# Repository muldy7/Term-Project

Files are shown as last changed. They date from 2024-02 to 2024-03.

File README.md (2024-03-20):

# Term-Project
Introduction 

This repository includes the code and documentation for the ME 405 Lab "Learn by Dueling" term project. The goal of this project was to create an automated foam dart turret to participate in a dueling competition. The turret had certain required functionality including the use of 1 brushed DC motor with encoder, another DC motor of the team's choice, and MLX90640 infrared camera supporting I2C communication. The turret is designed specifically for use in the ME 405 lab duel and operated by the team members. 

Hardware Design:  

The hardware system was designed to be robust and simple. Its main features include a panning axis controlled by a brushed DC motor with encoder feedback, a manually adjusted tilt secured by a bold, and servo-controlled trigger activation. The blaster used is a Nerf Strongarm revolving magazine and is manually cocked before each shot. The base is laser cut from 1/8th inch acrylic sheet and secures the motor and turntable relative to each other. The motor housing, gears, panning structure, camera mount, and trigger arm are 3D printed PLA. The camera was attached to the robot using the rail on the Nerf gun, along with 3D printed parts and a GoPro mount.  

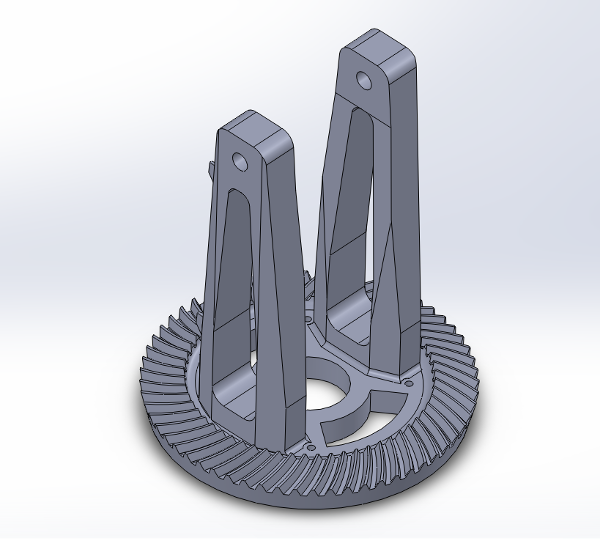
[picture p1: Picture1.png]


Figure 1: SolidWorks model of the turret base with a built-in bevel gear for rotation 

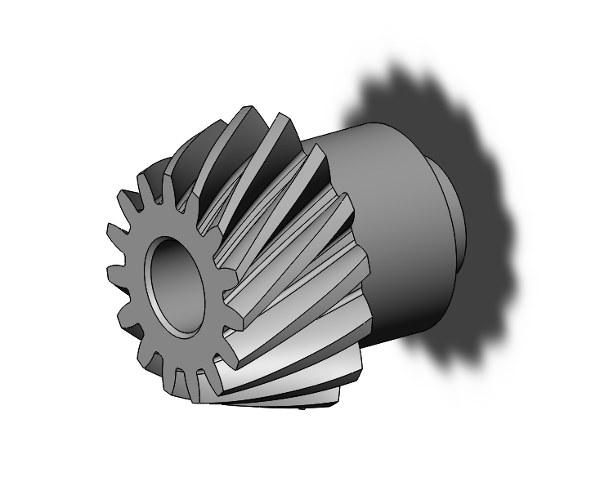
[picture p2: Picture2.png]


Figure 2: Pinion for the assembly 

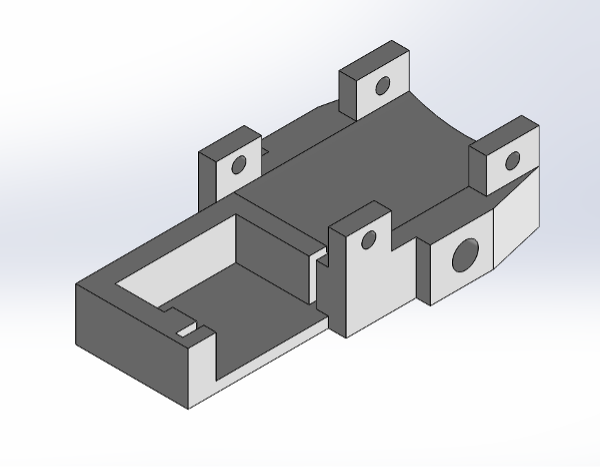
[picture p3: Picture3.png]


Figure 3: SolidWorks model of our Nerf gun mount  

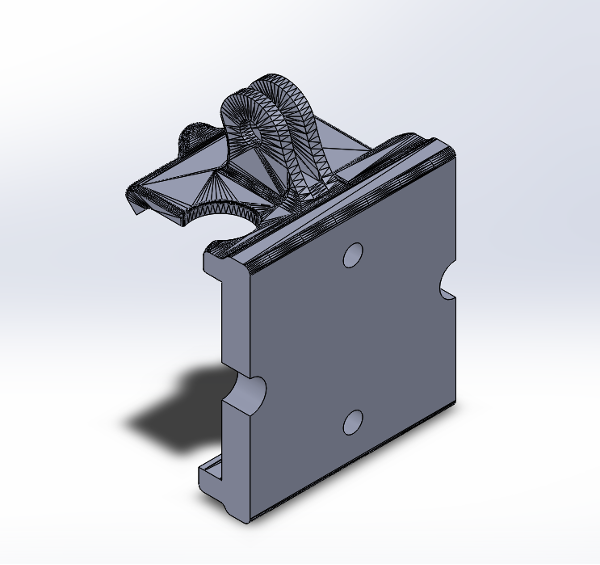
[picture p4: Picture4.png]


Figure 4: SolidWorks model of our camera mount  

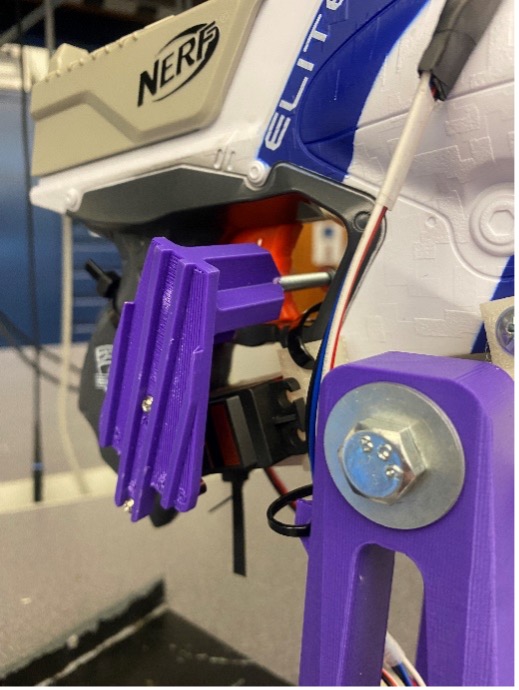
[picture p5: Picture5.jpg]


Figure 5. Trigger pull mechanism 

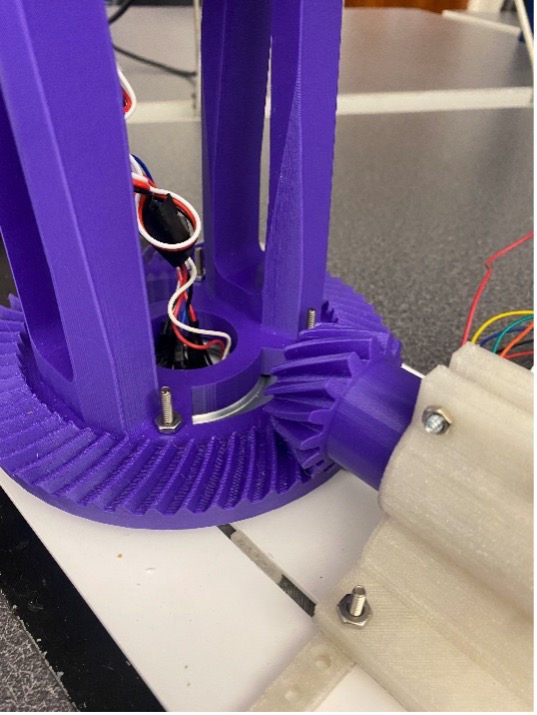
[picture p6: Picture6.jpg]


Figure 6. Panning axis mechanism. DC motor to panning structure on rotatory bearing.  

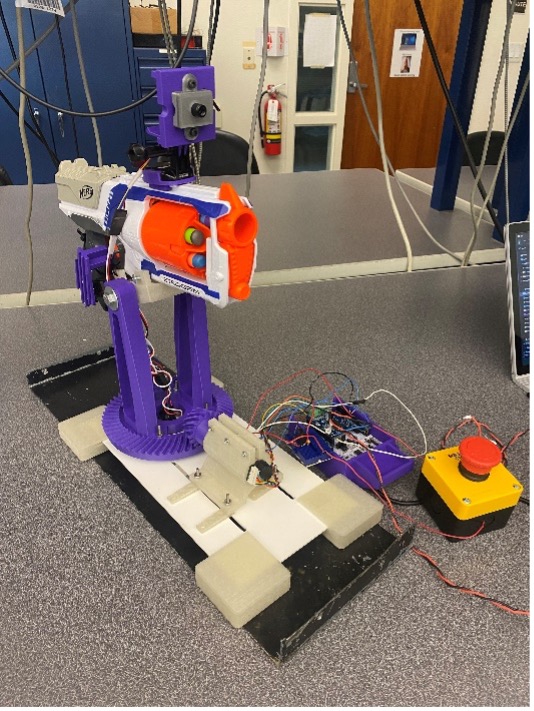
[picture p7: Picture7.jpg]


Figure 7. Entire hardware system 

Other hardware implementations include the addition of an emergency stop button and voltage regulator for the servo. The voltage regulator was used to supply the servo with 6V without the need for a second voltage source. The circuit was implemented as shown below with the input as 12V from the voltage source and the output to the servo.  

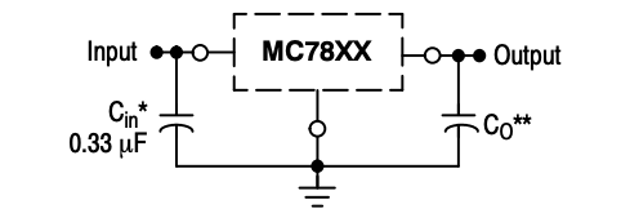
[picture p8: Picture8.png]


Source: https://www.mouser.com/datasheet/2/308/1/MC7800_D-2315963.pdf 

Software Design:   

The software includes a main file which implements cooperative multitasking and integrates all classes and functions created previously to use the hardware.  

The hardware classes are the encoder reader, motor drover, MLX cam, and servo driver. A PD controller class was created and used for the closed loop motor control.   

The main files include a camera task and a controller class which are implemented as finite state machines with cooperative multitasking using the task_share.py and cotask.py classes provided.  

The main file was designed around the finite state machines seen below. There were two main tasks in the file, one to control the turret and the other to take images with the camera.  The two tasks were designed to run through one cycle after the main program is run. 

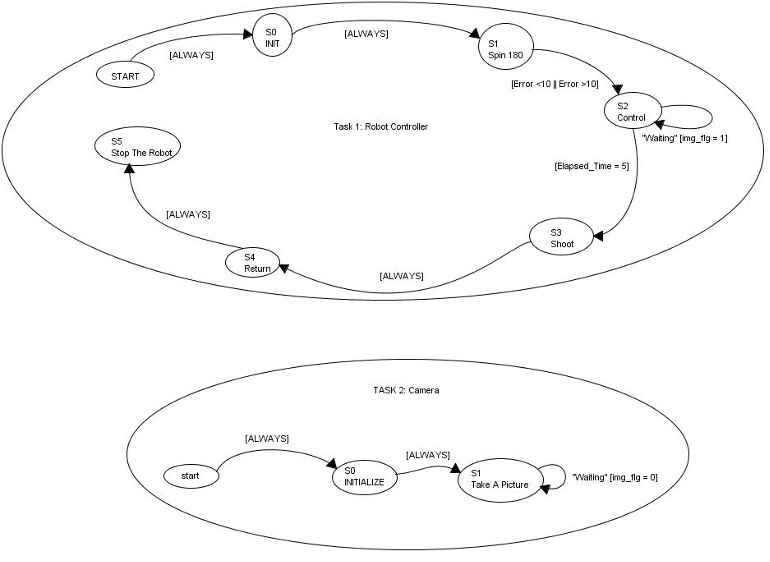
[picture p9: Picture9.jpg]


Figure: 8. Finite State Machines for the two tasks. 

Results: 

The robot won lab section 05 single elimination dueling tournament by eliminating 3 opposing teams. In each successive round our accuracy increased as we changed the algorithm parameters. The scoring criteria are as follows: First team to hit=3 points, second team to hit=1 point, no shoot=0 points, miss=-1. In the first round we scored net 0 points, and the last round we scored a net 8 points in 5 rounds.  

The following day during open competition, our robot remained undefeated and successfully hit opposing teams 10/12 times.  

We learned that the most important aspect to competition success was refinement of the targeting algorithm. Through the closed loop motor control, the gun was able to aim very accurately where it “wanted” but having this setpoint agree with the human target location was difficult. To have the setpoint algorithm more accurately find the target, a few additions were made to the algorithm.  One included limiting the field of view of the camera to above the table and within the left and right edges. Also, a filter was applied to all thermal data to eliminate any values lower than 300 to reduce background noise affecting the targeting. Lastly, the final setpoint was calculated based on a 5 columns centroid calculation around the hottest column of thermal data.  

This project has a lot of potential for future work and development, including improvements to the cooperative multitasking for more continuous feedback and thermal data processing. Also, a tilt axis for a full range of aiming would be a great hardware improvement.

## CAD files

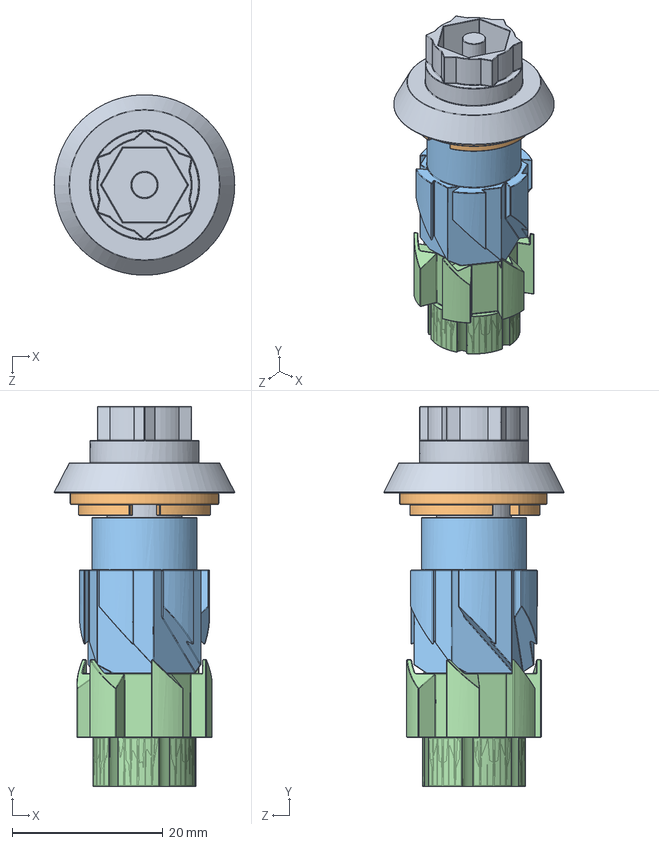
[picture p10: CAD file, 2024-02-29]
3D_models/nerf gun/Assem1.SLDASM
24.0 x 50.5 x 24.0 mm
Spin Lock
Spin Ring
Rotation 2
Rotation 1

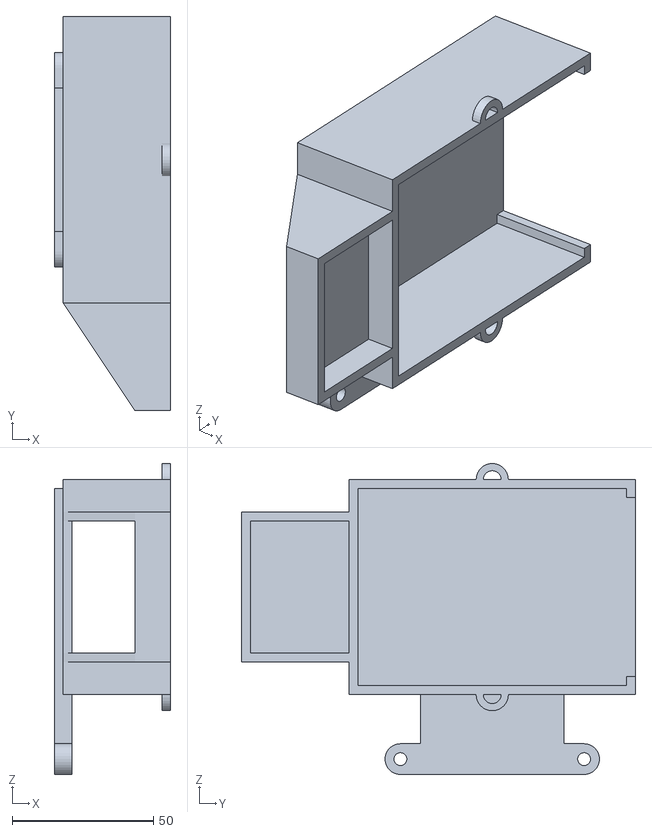
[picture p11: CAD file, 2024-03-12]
3D_models/assembly/CPU Holder v4.stl
41.3 x 139.7 x 110.2

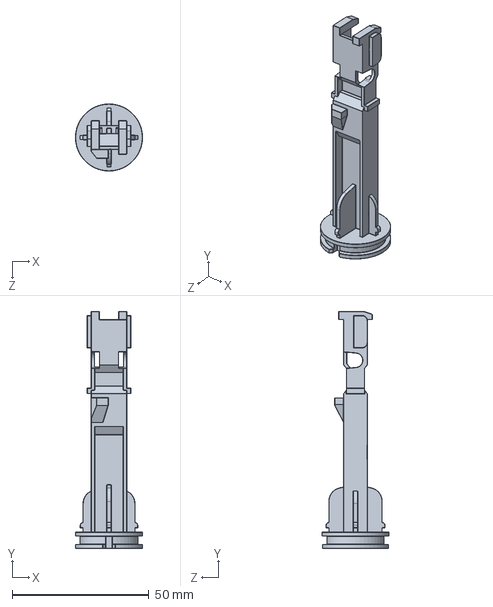
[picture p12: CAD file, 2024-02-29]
3D_models/nerf gun/Tower.SLDPRT
24.5 x 86.5 x 24.5 mm

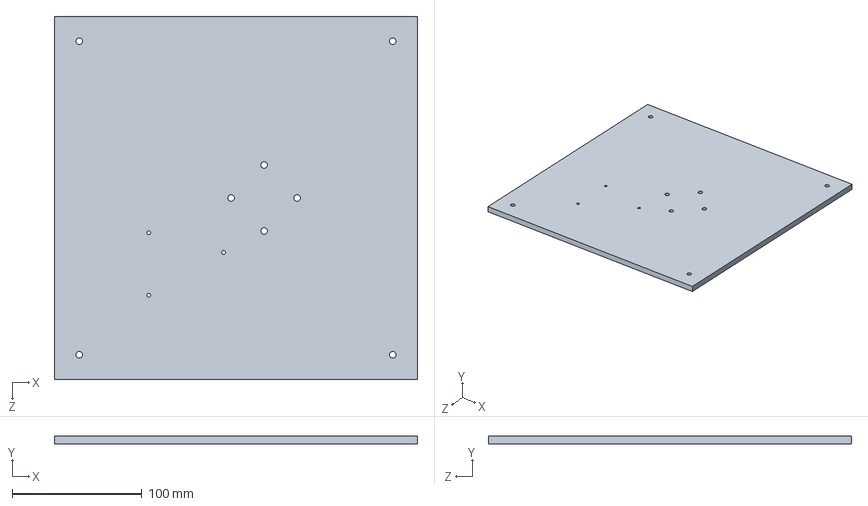
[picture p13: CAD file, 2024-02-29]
3D_models/assembly/box_base.SLDPRT
279.4 x 6.35 x 279.4 mm

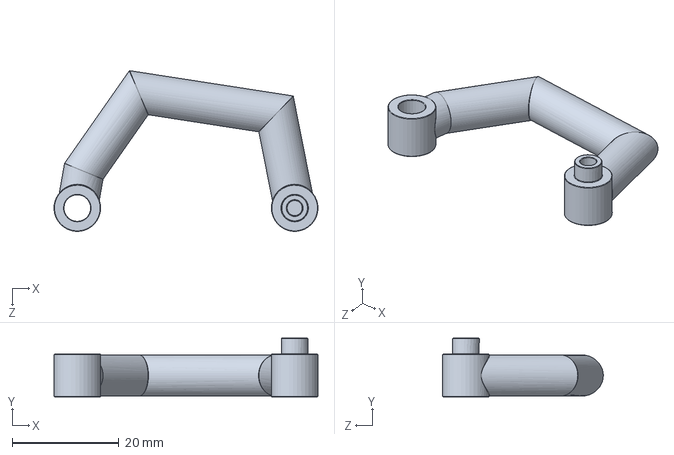
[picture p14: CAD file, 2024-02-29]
3D_models/nerf gun/Clasp.SLDPRT
49.5 x 11.0 x 30.1 mm

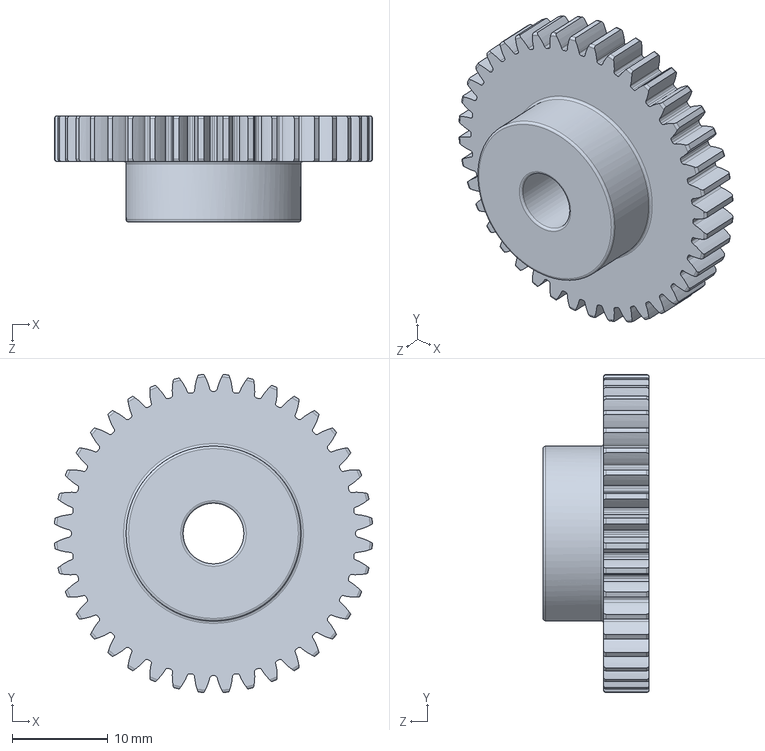
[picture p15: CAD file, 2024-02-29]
3D_models/assembly/pinion_for_rack.SLDPRT
33.3 x 33.3 x 11.1 mm

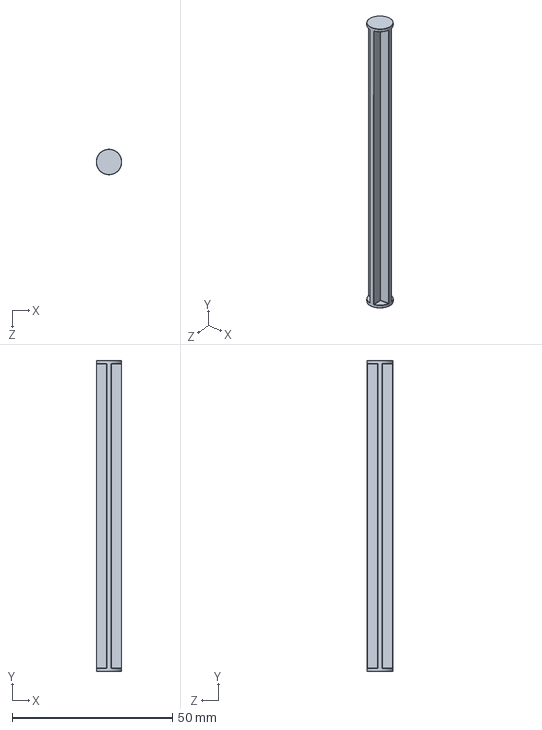
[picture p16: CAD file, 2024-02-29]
3D_models/nerf gun/Barrel Pole.SLDPRT
7.94 x 97.0 x 8.00 mm

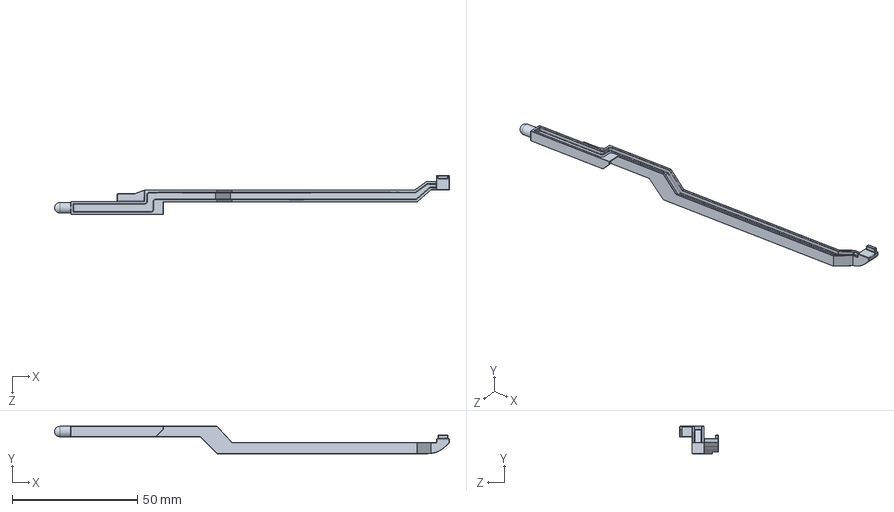
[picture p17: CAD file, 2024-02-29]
3D_models/nerf gun/Stretched Pipe.SLDPRT
157.9 x 11.0 x 15.5 mm

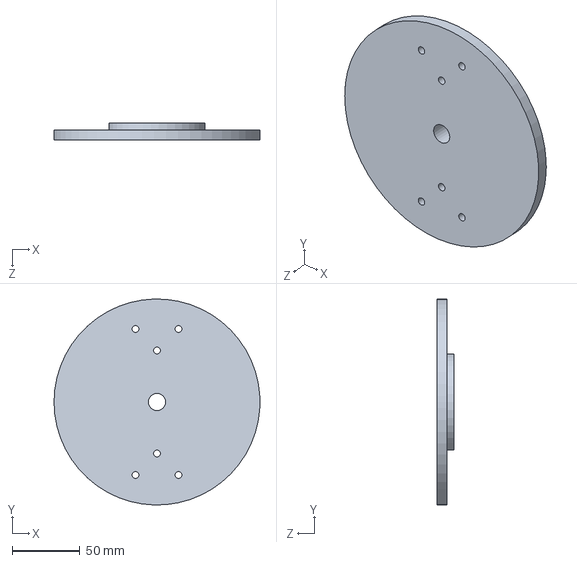
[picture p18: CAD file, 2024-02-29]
3D_models/assembly/pivot_base.SLDPRT
152.4 x 152.3 x 12.7 mm

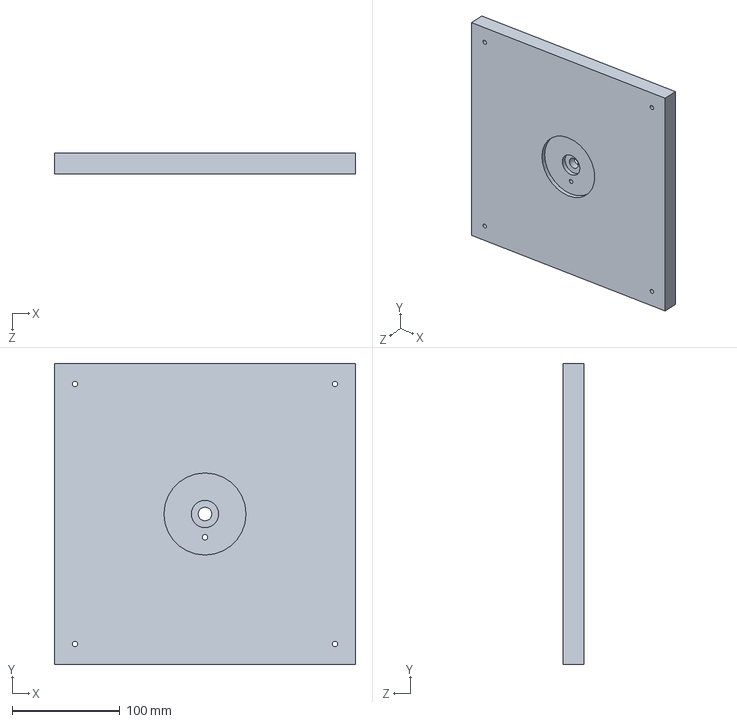
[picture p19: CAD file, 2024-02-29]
3D_models/assembly/box_top.SLDPRT
279.4 x 279.4 x 19.1 mm

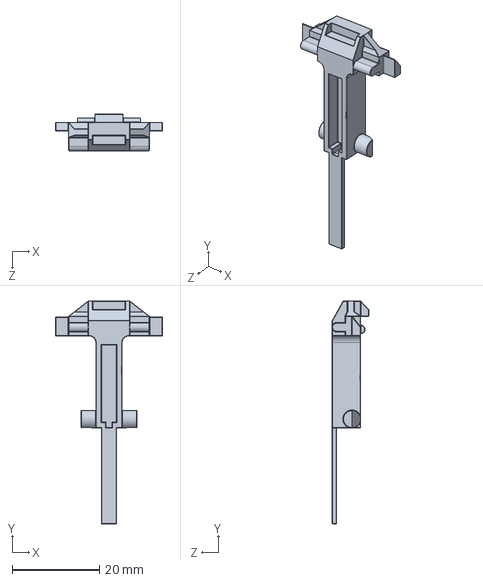
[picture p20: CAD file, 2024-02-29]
3D_models/nerf gun/T Piece.SLDPRT
24.5 x 51.0 x 8.37 mm

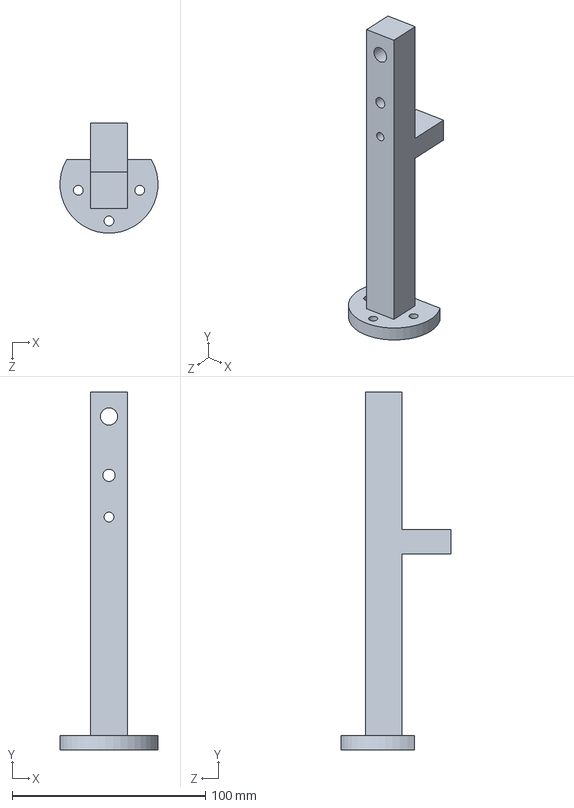
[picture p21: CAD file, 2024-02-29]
3D_models/assembly/pivot_arm.SLDPRT
50.7 x 185.4 x 57.1 mm

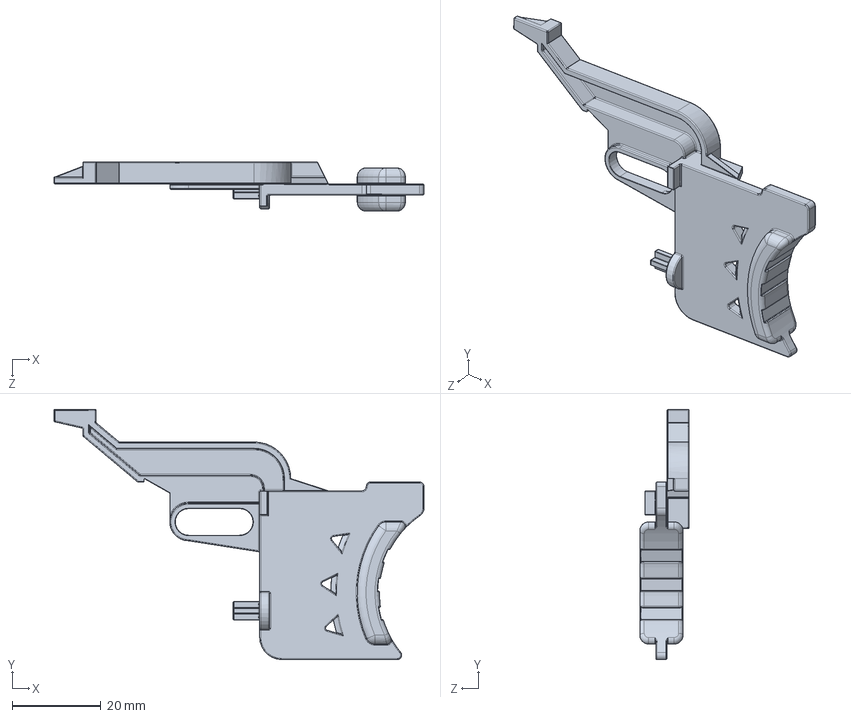
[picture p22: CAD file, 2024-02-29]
3D_models/nerf gun/Trigger 2.SLDPRT
83.3 x 56.3 x 11.1 mm

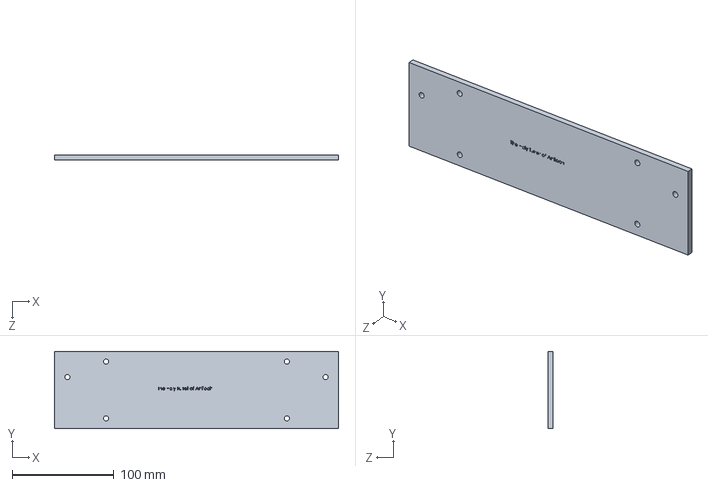
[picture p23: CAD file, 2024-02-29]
3D_models/assembly/box_side.SLDPRT
279.4 x 76.2 x 5.08 mm

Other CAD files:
3D_models/assembly/gun_holder.SLDPRT
3D_models/nerf gun/Hammer part.SLDPRT
3D_models/assembly/gear_rack.SLDPRT
3D_models/nerf gun/Spin Lock.SLDPRT
3D_models/assembly/box_support.SLDPRT
3D_models/assembly/nerf_holder.SLDPRT
3D_models/assembly/part_list.SLDDRW
3D_models/assembly/pivot_arm.SLDDRW
3D_models/assembly/trigger_puller.SLDPRT
3D_models/mcmaster stl files/2662N22_20 Degree Pressure Angle Plastic Gear.sldprt
3D_models/mcmaster stl files/2662N44_20 Degree Pressure Angle Plastic Gear.sldprt
3D_models/mcmaster stl files/90145A572_18-8 Stainless Steel Dowel Pin.sldprt
3D_models/mcmaster stl files/90145A824_18-8 Stainless Steel Dowel Pin.sldprt
3D_models/mcmaster stl files/fake_motor.SLDPRT
3D_models/mcmaster stl files/motor_holder.SLDPRT
3D_models/nerf gun/3 screw hole.SLDPRT
3D_models/nerf gun/Barrel Mount.SLDPRT
3D_models/nerf gun/Barrel slot.SLDPRT
3D_models/nerf gun/Bullet.SLDPRT
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

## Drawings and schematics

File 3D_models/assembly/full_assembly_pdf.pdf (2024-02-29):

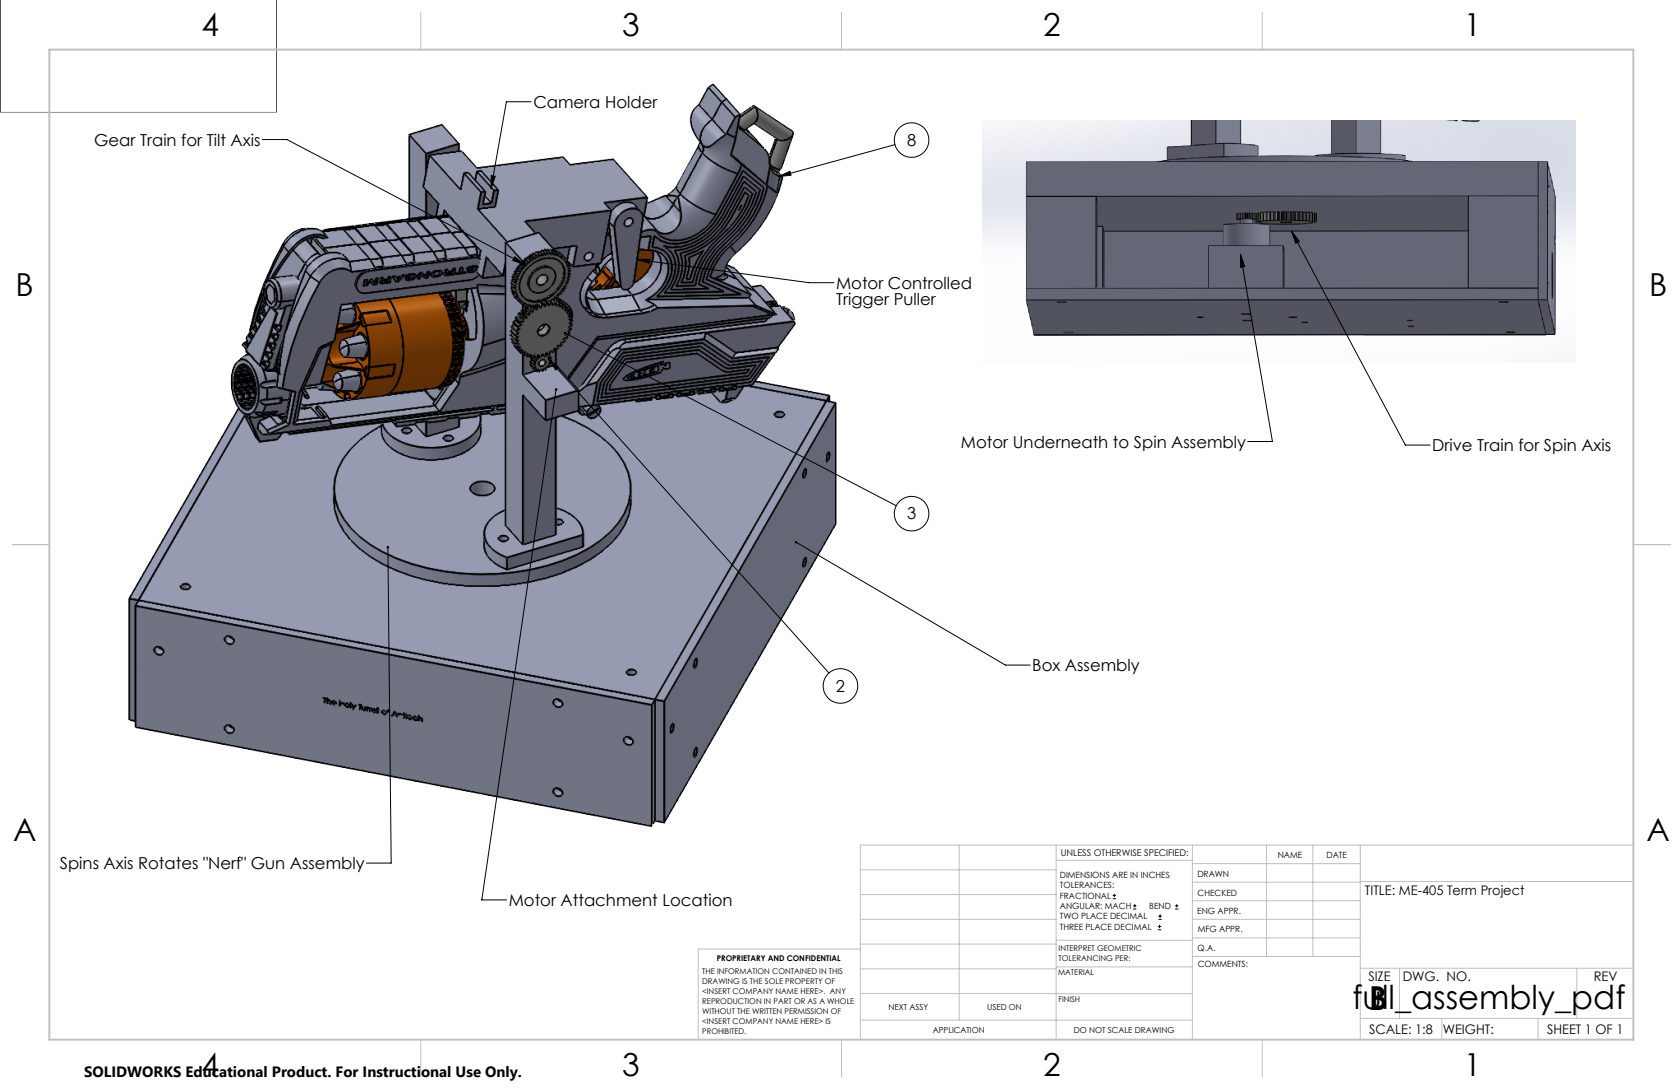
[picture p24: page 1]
Motor Controlled Trigger Puller; Camera Holder; Box Assembly

Gear Train for Tilt Axis

Motor Underneath to Spin Assembly

Drive Train for Spin Axis

Spins Axis Rotates "Nerf" Gun Assembly

UNLESS OTHERWISE SPECIFIED: | | NAME | DATE
DIMENSIONS ARE IN INCHES TOLERANCES: FRACTIONAL ANGULAR: MACH BEND TWO PLACE DECIMAL THREE PLACE DECIMAL | DRAWN

CHECKED | | | TITLE: ME-405 Term Project

Motor Attachment Location

ENG APPR.
MFG APPR.

INTERPRET GEOMETRIC TOLERANCING PER: | Q.A.
MATERIAL | full_assembly_pdf | SIZE B | DWG. NO. | REV

PROPRIETARY AND CONFIDENTIAL
THE INFORMATION CONTAINED IN THIS
DRAWING IS THE SOLE PROPERTY OF
<INSERT COMPANY NAME HERE>. ANY
REPRODUCTION IN PART OR AS A WHOLE
WITHOUT THE WRITTEN PERMISSION OF
<INSERT COMPANY NAME HERE> IS
PROHIBITED.

NEXT ASSY | USED ON | FINISH

APPLICATION | DO NOT SCALE DRAWING | | SCALE: 1:8 | WEIGHT: | SHEET 1 OF 1

SOLIDWORKS Educational Product. For Instructional Use Only.

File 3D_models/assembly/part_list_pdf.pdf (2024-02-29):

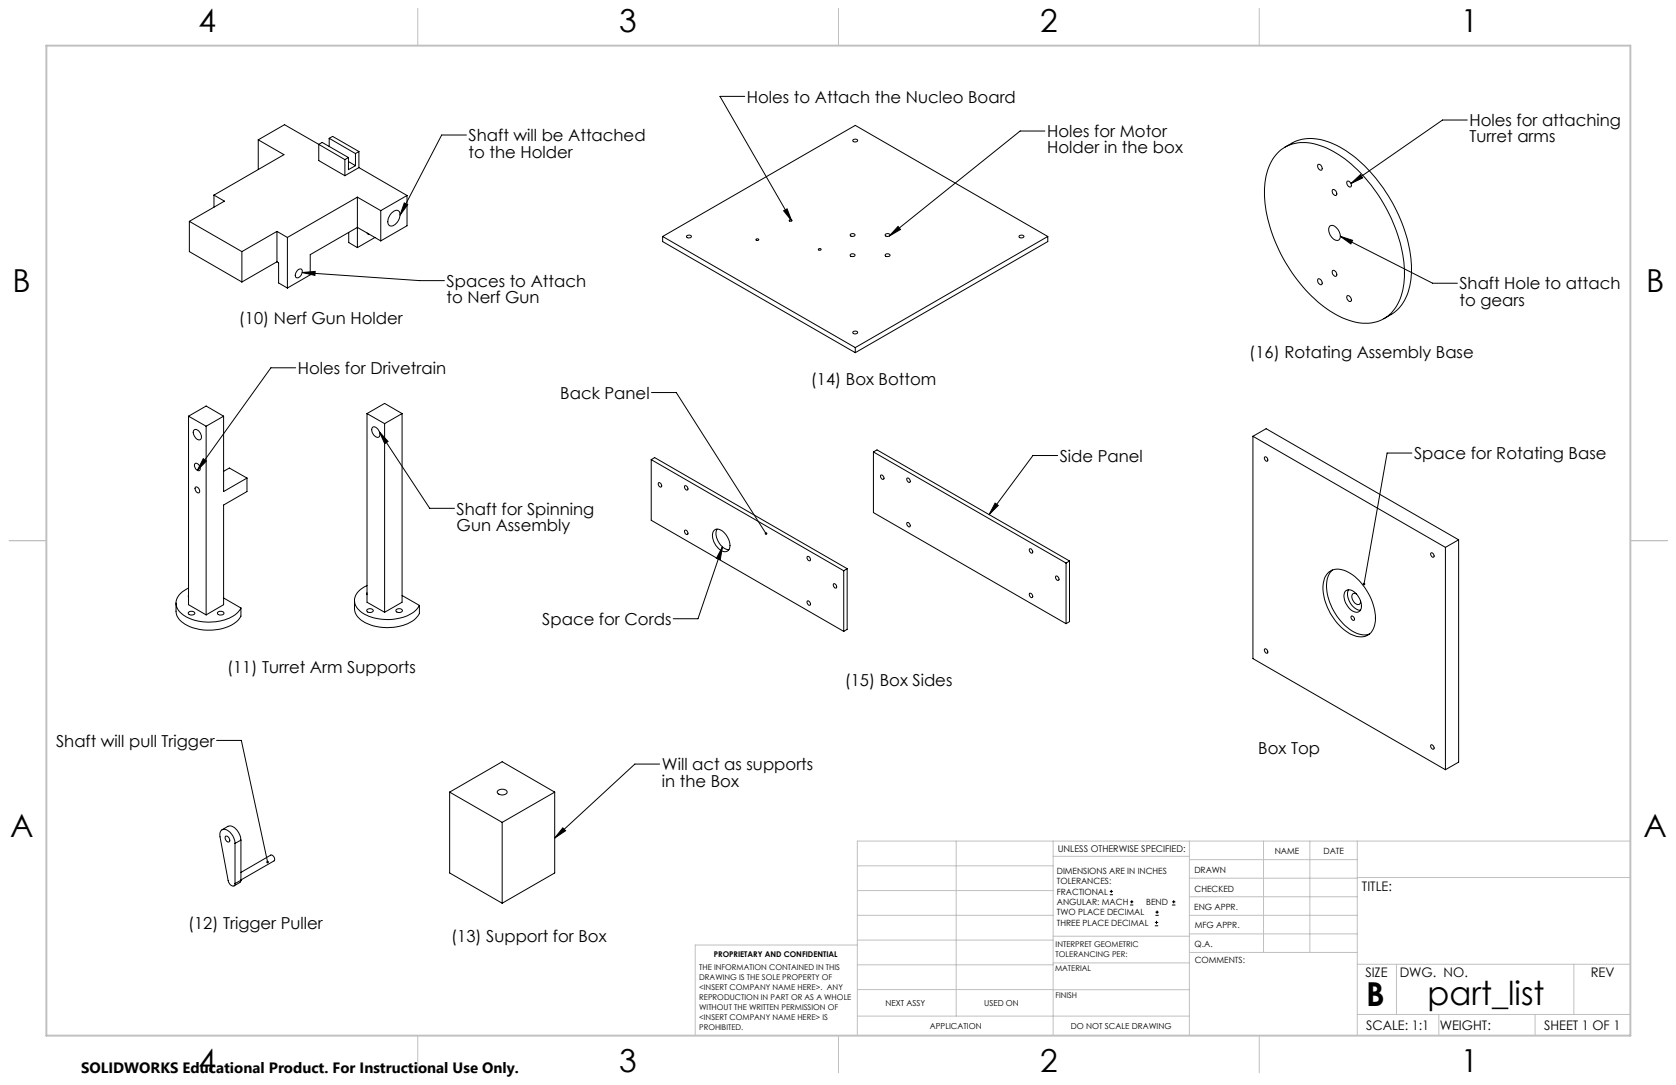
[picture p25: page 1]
(14) Box Bottom; Back Panel; Side Panel; Box Top; (12) Trigger Puller; (15) Box Sides

Holes to Attach the Nucleo Board

Holes for attaching
Turret arms

Holes for Motor
Holder in the box

Shaft will be Attached
to the Holder

Spaces to Attach
to Nerf Gun

Shaft Hole to attach
to gears

(10) Nerf Gun Holder

(16) Rotating Assembly Base

Holes for Drivetrain

Space for Rotating Base

Shaft for Spinning
Gun Assembly

Space for Cords

(11) Turret Arm Supports

Shaft will pull Trigger

Will act as supports
in the Box

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

CHECKED | | | TITLE:

ENG APPR.
MFG APPR.

(13) Support for Box

INTERPRET GEOMETRIC TOLERANCING PER: | Q.A.
MATERIAL | | SIZE B | DWG. NO. part_list | REV

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

NEXT ASSY | USED ON | FINISH

APPLICATION | DO NOT SCALE DRAWING | | SCALE: 1:1 | WEIGHT: | SHEET 1 OF 1

SOLIDWORKS Educational Product. For Instructional Use Only.

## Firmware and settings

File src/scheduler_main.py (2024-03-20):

"""!
@file scheduler_main.py
    This file contains our main code to set-up the scheduler to run our robot.
    Although we were able use this file to run our code cooperatively, we found that the non scheduled code worked better for the competition. 
    This scheduled code breaks the function into two tasks, the Thermal Camera Task and The Robot Controller Task. 

@author JR Ridgely, Abe Muldrow, Lucas Rambo, Peter Tomson
@date February 29, 2024 
@copyright (c) 2015-2021 by JR Ridgely and released under the GNU
    Public License, Version 2. 
"""

import gc
import pyb
import cotask
import task_share
from pd_controller import PD_Controller
from servo_driver import ServoDriver
from controller import Controller
from motor_driver import MotorDriver
from encoder_reader import EncoderReader
import utime
from mlx_cam import MLX_Cam
from machine import Pin, I2C


def task1_fun(shares):
    """!
    Task that controls the motion of the robot using the motor controlling the pan axis and the servo to pull the trigger. 
    The task uses the share for the image_flag value and new values of camera_error used in the control loop. 
    Each camera_error tells the device a new location to spin to for finding the target. 
    This task sets image_flag to 1 initially so no pictures are taken, then sets to zero every time the device has moved to
    the new setpoint. This allows the device to move multiple times and adjust before FREEZE is called. After 5 seconds 
    has passed the code then transitions to pull the trigger. 

    @param shares A list holding the share and queue used by this task
    """
    # Get references to the share and queue which have been passed to this task
    i_flg, cam_set = shares    # set up the local variables for the shares
    
    #setting up the FSM
    s0_init=0
    s1_spin=1
    s2_control=2
    s3_shoot=3
    s4_return=4
    s5_stop=5

    state=0

    while True:
        print(state)
        # STATE 0: INIT
        if state==s0_init:
            #instantiate the hardware 
            motor1=MotorDriver('PC1','PA0','PA1',5)

            encoder1=EncoderReader('PC6','PC7',8)   

            controller1=PD_Controller(6560,1,0.015,encoder1)   # set up initial control parameters for the 180 degree rotate

            servo1=ServoDriver('PA5',2,1)
            
            # interstate variables
            # count = 0   # for counting in the control loop

            time_start = utime.time()
            
            i_flg.put(1)    # set to one if we 
            cam_set.put(0)

            # set the next state
            state=s1_spin
            yield
        

        # STATE 1: SPIN 180 DEGREES
        elif state == s1_spin:
            # loop to control the motor to spin 180 degrees
            for i in range(150):    
                controller1.output_fun.read()    # run the controller
                meas_output=controller1.output_fun.pos   # set the measured output
                controller1.run(-1*meas_output)    # run the controller with the new measured output
                PWM=controller1.PWM # set a new PWM from the conroller run function
                motor1.set_duty_cycle(PWM)  # set the PWM of the motor to the new PWM value
                    
                # print out for testing
                print(i,PWM,controller1.err)
                yield
                # exit the loop once the error is small enough
                if controller1.err <= 10 and controller1.err >= -10:
                        
                    motor1.set_duty_cycle(0)
                    #utime.sleep_ms(10)	# wait 0.10 ms before moving to next state
                    controller1.reset_loop()	# reset the controller
                    controller1.output_fun.zero()	# zero the encoder
                    controller1.set_setpoint(0) # reset set point
                    i_flg.put(0)    # tell the camera we are ready for an image
                    
                    # move to the next state
                    state=s2_control	
                    #utime.sleep(3)
                    break
                elif i == 149:  # if error never gets small enough leave the loop
                    motor1.set_duty_cycle(0)
                    #utime.sleep_ms(10)	# wait 0.10 ms before moving to next state
                    controller1.reset_loop()	# reset the controller
                    controller1.set_setpoint(0)
                    controller1.output_fun.zero()	# zero the encoder
                    i_flg.put(0)    # tell the camera we are ready for an image

                    # move to the next state
                    state=s2_control	
                    #utime.sleep(3)
                    break
                else:
                    yield   # yield if still looping
            
            yield


        # STATE 2: CONTROL THE MOTOR FOR 6 SECONDS
        elif state==s2_control:

            # change gain values for the controller for small movements
            controller1.set_Kp(1.15)	
            controller1.set_Kd(.01575)

            # before controller the motor, test if there is a new image
            img_flg = i_flg.get()
            while img_flg == 0:
                img_flg = i_flg.get()
                camera_error = cam_set.get()
                controller1.set_setpoint(camera_error)
                controller1.output_fun.zero()
                controller1.reset_loop()   # need to test if this is necessary or not
                print('waiting for image in the control loop')
                
                yield 
            
            # the control loop for the camera controller
            for i in range(150):
                # the control loop
                controller1.output_fun.read()    # run the controller
                meas_output=controller1.output_fun.pos   # set the measured output
                controller1.run(-1*meas_output)    # run the controller with the new measured output
                PWM=controller1.PWM     # set a new PWM from the conroller run function
                motor1.set_duty_cycle(PWM)  # set the PWM of the motor to the new PWM value
                    
                # print out for testing
                print(i,PWM,controller1.err)

                # calculate the elapsed time, want to exit the loop after 5 seconds
                curr_time = utime.time()
                elap_time = curr_time - time_start

                # exit the loop once the error is small enough
                if (controller1.err <= 10 and controller1.err >= -10) or i == 149:
                        
                    motor1.set_duty_cycle(0)
                    #utime.sleep_ms(10)	# wait 0.10 ms before moving to next state
                    controller1.reset_loop()	# reset the controller
                    controller1.output_fun.zero()	# zero the encoder
                    controller1.set_setpoint(0) # reset set point

                    # tell the camera we are ready for an image
                    i_flg.put(0)       # reset the flags
                    img_flg = 0        

                    # only exit once the error is small enough even if its been longer than 5 seconds
                    if elap_time >= 5:
                        print('shooting!')
                        
                        state=s3_shoot
                    break
            yield


        # STATE 3: Shoot the Target       
        elif state==s3_shoot:
            
            # pull the trigger
            print('pulling the trigger!')
            servo1.set_pos(160)	# move the servo into position
            utime.sleep(1)	# wait
            servo1.set_pos(195)	# pull the trigger
            utime.sleep(1)	# wait
            servo1.set_pos(160)	# pull it back

            # set the state to the return to zero_state
            state=s4_return
            yield

        
        #STATE 4: Return to Zero
        elif state==s4_return:
            motor1.set_duty_cycle(0)    # stop the robot from moving

            # set the setpoint to negative 180 degrees
            neg_setpoint = -1*6560
            controller1.set_setpoint(neg_setpoint)

            # set the new gains
            controller1.set_Kp(0.1)
            controller1.set_Kd(0)

            # same loop as the 180 spin as seen before
            for i in range(150):    
                controller1.output_fun.read()    # run the controller
                meas_output=controller1.output_fun.pos   # set the measured output
                controller1.run(-1*meas_output)    # run the controller with the new measured output
                PWM=controller1.PWM     # set a new PWM from the conroller run function
                motor1.set_duty_cycle(PWM)  # set the PWM of the motor to the new PWM value
                    
                # print out for testing
                print(i,PWM,controller1.err)
                    
                # exit the loop once the error is small enough
                if (controller1.err <= 10 and controller1.err >= -10) or i == 149:  # or once theres been a full rotation in case of steady state error
                    
                    motor1.set_duty_cycle(0)    # stop the motor
    
                    # move to the next state
                    state=s5_stop
                    break
                    #yield
            yield

            
        # STATE 5: Stop the Robot
        else:
            motor1.set_duty_cycle(0)
            
            # print final values for verification
            # print final camera_error
            print(camera_error)

            print('finished with destorying my enemies!')
            break
        
            
# TASK 2: CAMERA TASK
def task2_fun(shares):
    """!
    Task for taking a picture. The task takes a picture every time the image_flag from the share is 0. The camera then sets the 
    flag to 1 to tell the control task that there is a new image with a camera_error value for moving the device. 

    @param shares A tuple of a share and queue from which this task gets data
    """
    # Get references to the share and queue which have been passed to this task
    i_flg_cam, cam_set_cam = shares

    state = 0

    while True:
        # STATE 0: INIT
        if state == 0:
            # camera set-up code
            try:
                # The following import is only used to check if we have an STM32 board such
                # as a Pyboard or Nucleo; if not, use a different library
                from pyb import info    

                # Oops, it's not an STM32; assume generic machine.I2C for ESP32 and others
            except ImportError:
                # For ESP32 38-pin cheapo board from NodeMCU, KeeYees, etc.
                i2c_bus = I2C(1, scl=Pin(22), sda=Pin(21))

                # OK, we do have an STM32, so just use the default pin assignments for I2C1
            else:
                i2c_bus = I2C(1)

            print("MXL90640 Easy(ish) Driver Test")

            # Select MLX90640 camera I2C address, normally 0x33, and check the bus
            i2c_address = 0x33
            scanhex = [f"0x{addr:X}" for addr in i2c_bus.scan()]
            print(f"I2C Scan: {scanhex}")

                # Create the camera object and set it up in default mode
            camera = MLX_Cam(i2c_bus)
            print(f"Current refresh rate: {camera._camera.refresh_rate}")
            camera._camera.refresh_rate = 10.0  # can try faster refresh rates
            print(f"Refresh rate is now:  {camera._camera.refresh_rate}")
            
            # set the next state
            state=1
            yield
        
        # STATE 1: Take a picture
        else:
            img_flg = i_flg_cam.get()
            
            if img_flg == 0:   # wait for image flag to be true
            
                image = None # reset image
                while not image:
                    image = camera.get_image_nonblocking()
                    print('waiting for image')

                    yield 
                
                
                # test prints
                print('took a picture!')
                    
                centroid = True # if True do the centroid calculation for our camera to find i_bar

                # find the hotspot and put it in the share 
                camera.get_hotspot(image, centroid, limits=(0, 1000))   # use the hotspot calculation to find the target
                cam_set_cam.put(camera.camera_error)    # put the calculated encoder tics in the share

                # lower the flag
                i_flg_cam.put(1)	# reset the shared flag variable
                img_flg = 1		# reset the local flag variable
                
                yield

            else:
                # yield and wait for the motor task if img_flg == 1
                yield
       
        

# This code creates a share, a queue, and two tasks, then starts the tasks. The
# tasks run until somebody presses ENTER, at which time the scheduler stops and
# printouts show diagnostic information about the tasks, share, and queue.
if __name__ == "__main__":

    # Create intertask variables for the loops
    # share for the camera_error variable, the setpoint from the hotspot
    camera_setpoint = task_share.Share('f', thread_protect=False, name="Camera Setpoint Share")   # f for float 

    # flag for communicating if an image is required
    # img_flg == 1 means there has been a new image for the controller task
    image_flag = task_share.Share('h', thread_protect=False, name="Image Flag Share")      

    # Create the tasks. If trace is enabled for any task, memory will be
    # allocated for state transition tracing, and the application will run out
    # of memory after a while and quit. Therefore, use tracing only for alw
    # debugging and set trace to False when it's not needed

    # task1 is the motor and servo controlling task
    task1 = cotask.Task(task1_fun, name="Motor and Servo Control", priority=1, period=5,    # could be much lower for our loop depending on precision
                        profile=True, trace=False, shares=(image_flag, camera_setpoint))
    
    # task2 is the imager for the camera
    task2 = cotask.Task(task2_fun, name="Thermal Camera Imager", priority=2, period=100, # should experiment with the period
                        profile=True, trace=False, shares=(image_flag, camera_setpoint))
    
    cotask.task_list.append(task1)
    cotask.task_list.append(task2)
    
    # Run the memory garbage collector to ensure memory is as defragmented as
    # possible before the real-time scheduler is started
    gc.collect()

    # Run the scheduler with the chosen scheduling algorithm. Quit if ^C pressed
    while True:
        try:
            cotask.task_list.pri_sched()
        except KeyboardInterrupt:
            break

    # Print a table of task data and a table of shared information data
    print('\n' + str (cotask.task_list))
    print(task_share.show_all())
    print(task1.get_trace())
    print('')

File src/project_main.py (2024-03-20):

"""!
@file project_main.py

-The Holy Turrent of Antioch-

This is the file we used during the Department of Foamland Securitiy Automated Sentry Trials.
It contains code to rotate the turret 180 degrees, locate a target using a calculated heat signature, and fire at them.
This was the main file used that contains calls to other python classes that are used for this project.
Those files will contain a more in-depth description of each of their actions.
This code was set up to run as a Finite State Machine, once through.
Afterwards, the user would need to re-run the code in order to shoot again.

See the Scheduler code for a working cooperative program.
We found that while it worked, there wasn't too much of a difference compared to this file and the non-scheduler code 
performed better in the context of the competition. 

@author Abe Muldrow
@author Lucas Rambo
@author Peter Tomson

@date March 8th, 2024
"""
from pd_controller import PD_Controller
from servo_driver import ServoDriver
#from controller import Controller # the old controller class can still be used, but this device was implemented with PD control
from motor_driver import MotorDriver
from encoder_reader import EncoderReader
import utime
from mlx_cam import MLX_Cam
import gc
from machine import Pin, I2C

#FSM States
s0_init=0
s1_rotate=1
s2_control=2
s3_shoot=3
s4_stop=4

state=0

while True:
        print('state: ' + str(state))
      
                # STATE 0: INIT
        if state==s0_init:
            # initiate the hardware 
            motor1=MotorDriver('PC1','PA0','PA1',5)

            encoder1=EncoderReader('PC6','PC7',8)   

            controller1=PD_Controller(6560,.4,0.0185,encoder1)  # set the gain values for the first control loop

            servo1=ServoDriver('PA5',2,1)
        
            # camera set-up code
            # this code is taken from the mlx_cam file that was given to us
            try:
                # The following import is only used to check if we have an STM32 board such
                # as a Pyboard or Nucleo; if not, use a different library
                from pyb import info    

                # Oops, it's not an STM32; assume generic machine.I2C for ESP32 and others
            except ImportError:
                    # For ESP32 38-pin cheapo board from NodeMCU, KeeYees, etc.
                i2c_bus = I2C(1, scl=Pin(22), sda=Pin(21))

                # OK, we do have an STM32, so just use the default pin assignments for I2C1
            else:
                i2c_bus = I2C(1)

            print("MXL90640 Easy(ish) Driver Test")

            # Select MLX90640 camera I2C address, normally 0x33, and check the bus
            i2c_address = 0x33
            scanhex = [f"0x{addr:X}" for addr in i2c_bus.scan()]
            print(f"I2C Scan: {scanhex}")

            # Create the camera object and set it up in default mode
            camera = MLX_Cam(i2c_bus)
            print(f"Current refresh rate: {camera._camera.refresh_rate}")
            camera._camera.refresh_rate = 10.0	# could increase this for faster photos
            print(f"Refresh rate is now:  {camera._camera.refresh_rate}")
            
            # transition to the next state, ALWAYS
            state=s1_rotate
        

        # STATE 1: Rotate 180 Degrees
        elif state==s1_rotate:
                # this state is for rotating the machine 180 degrees, implemented with a for loop
    
                for i in range(150):    # each run should be at most 3000 miliseconds or 3 seconds, each run acts as a controller loop
                    utime.sleep_ms(10)  # sleep for 10 ms every control loop 
                    controller1.output_fun.read()    # run the controller
                    meas_output=controller1.output_fun.pos   # set the measured output
                    controller1.run(-1*meas_output)    # run the controller with the new measured output
                    PWM=controller1.PWM # set a new PWM from the conroller run function
                    motor1.set_duty_cycle(PWM)  # set the PWM of the motor to the new PWM value
                    
                    # print out for testing
                    print(i,PWM,controller1.err)
                    
                    # exit the loop once the error is small enough
                    if controller1.err <= 10 and controller1.err >= -10:
                        
                        motor1.set_duty_cycle(0)    # stop the motor
                        utime.sleep_ms(10)	# wait 0.10 ms before moving to next state
                        controller1.reset_loop()	# reset the controller
                        controller1.output_fun.zero()	# zero the encoder
                        
                        state=s2_control	# move to the next state, once error is smaller enough
                        utime.sleep(1.5)    # sleep to wait for FREEZE to be called
                        break
                    if i == 149:    # if error never gets small enough, the loop should still be exited
                        motor1.set_duty_cycle(0)
                        utime.sleep_ms(10)	# wait 0.10 ms before moving to next state
                        controller1.reset_loop()	# reset the controller
                        controller1.output_fun.zero()	# zero the encoder
                        
                        state=s2_control	# move to the next state
                        utime.sleep(1.5)    # sleep to wait for FREEZE to be called
                        break
                    
        # STATE 2: Find the Target
        elif state==s2_control:
                # this state waits for an image to be found from the camera, calculates where the target is using the get_hotspot function,
                # and then moves to the position of the target based on the encoder tics value returned by the get_hotspot function.
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

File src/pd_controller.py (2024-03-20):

'''!
@file pd_controller.py

This file implements pd control of our device with some small changes to the previous controller class. 
The Kd control is implemented with an addition to the control equation, along with code to calculate the
previous and change in error for Kd implementation. 

This file contains code to create a controller class that allows us to create a control loop to run our motor.
This controller class when used in conjuction with our motor_driver and encoder_reader classes allow use to implement 
closed loop porportional and derivative control of our motor. The class below includes function to init and run our controller, 
along with setting the setpoint, Kd, and Kp value of the control loop. An additional function is included to reset the controller
values for multiple control loops during our robot's use. 

@author Abe Muldrow
@author Lucas Rambo
@author Peter Tomson
@date 3/8/2024  
'''

class PD_Controller:
    
    def __init__ (self, setpoint, Kp, Kd, read_fun):
        """! 
        Creates a Controller Object by initializing a setpoint (a desired location for the motor)
        a Kp value given by a user, a Kd value given by a user, and a encoder read function from an Encoder Object.

        @param setpoint This is a location for the motor in units of encoder counts.
        @param Kp A control gain set by the user. This is used to produce the actuation signal for the motor.
        @param Kd a controller gain set by the user. This is used for the controller's Kd implementation. 
        @param read_fun This is a read function from an Encoder Object.

        """
        self.Kp = Kp
        self.setpoint = setpoint
        self.output_fun = read_fun
        self.pos_output = []
        self.Kd = Kd

        # values for Kd control
        # timer values used for calculating rate of change of error
        #self.prev_time = 0  # previous time looping
        #self.curr_time = 0  # current time looping
        
        self.T = 0   # this is the trigger rate for the controller
        self.delta_err = 0 # this store the change in error for derivative control, the first value should be error
        self.prev_err = 0 # previous error value for delta_err calculation

        self.err = 51 # for initilization, need an initial error for the control loop
        self.store = True    # for storing values, store values if self.True == True
        
    def run(self, meas_output):
        """!
        This function runs the controller and changes the PWM for the next cycle. 
        The control loop takes the input encoder tics from meas_output and runs it through the control loop.
        This control loop includes proportional and derivative control, meaning the Kp gain is multiplied by the current error
        and the Kd values is multiplied by the change in error. The products are then added together and the resulting value
        is the PWM sent to the motor. 
    
        @param meas_output This value is the previous measured output input to the controller function. 
                           The value of meas_output is in encoder tics and tracks the current position of the motor. 
        """
        # create the equation that runs the control loop
        # calculate error
        self.err = self.setpoint - meas_output

        # calculate delta error for Kd
        self.delta_err = self.err - self.prev_err

        # calculate the change in time, for Kd
        #self.curr_time = utime.time()
        #self.T = self.curr_time - self.prev_time
        self.T = 0.01 # rough estimate, in ms, of the board's trigger rate

        # calculate PWM
        # the equation below represents the control loop to calculate the required motor PWM 
        self.PWM = self.Kp*(self.err) + (self.Kd*(self.delta_err/self.T))    

        # store values for Kd calculation
        self.prev_err = self.err
        #self.prev_time = utime.time()

        # store values for graphing
        if self.store == True:  # if self.store == True store values for step-response graphing
            self.pos_output.append(meas_output)
        if len(self.pos_output) >= 1000:    # need to stop storing values if there are too many
            self.store = False  # set store to false
        
    
    def set_setpoint(self,setpoint):
        """!
        This function sets the setpoint for the controller object. The setpoint is in encoder tics and used in the control loop to 
        calculate error. 
    
        @param setpoint This is a location for the motor in units of encoder counts.
        """
        self.setpoint=setpoint  # store in the class object
        
    def set_Kp(self,Kp):
        """!
        This function sets the Kp value for the controller object. The Kp is the proportional gain used in the control loop. 
    
        @param Kp A control gain set by the user. This is used to produce the actuation signal.
        """
        self.Kp=Kp

    def set_Kd(self,Kd):
        """!
        This function sets the Kd value for the controller object. The Kd value is the derivative gain used in the control loop. 
    
        @param Kd A control gain set by the user. This is used to produce the actuation signal.
        """
        self.Kd=Kd
        
    def step_response(self):
        '''!
        This function allows the stored values from the control loop to be plotted for a step-response graph. 
        This function was used in the main.py file along with our gui code to plot different step-responses for testing. 
        '''
        print('start')  # print 'start' to tell the computer to be ready for values
        for i in range(len(self.pos_output)):
            print(i*3.333,self.pos_output[i]) # print each output value along with its time value, does a step about every 3 miliseconds
        print('end')    # print 'end' to tell the computer the values are ended
        
    def reset_loop(self):
        """!
        This function resets the calculations for a new control loop. 
        This function can be used in conjuction with encoderX.read() & set_setpoint() for a new control loop of a different angle

        """
        # reset variables for the Kd calculation
        self.delta_err = 0 # this store the change in error for derivative control, the first value should be error
        self.prev_err = 0 # previous error value for delta_err calculation

        # reset the timer
        #self.prev_time = 0  # previous time looping
        #self.curr_time = 0  # current time looping
       


    
    

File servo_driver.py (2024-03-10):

import micropython
import time
import pyb


class ServoDriver:
    def __init__ (self, servo_pin, timer_channel):

        servo_pin = getattr(pyb.Pin.board, servo_pin) # get the pin value for the pin store in en_pin
        timer_channel = getattr(pyb.Pin.board, timer_channel)
        
    
        self.servo_pin=pyb.Pin(servo_pin, pyb.Pin.OUT_PP, value=0)   #initialize the pin as output pin
        t = pyb.Timer(timer_channel, freq=1000) #start the timer 
        t.prescaler(80) #set prescaler to get clock frquency to 1 Mhz, not 80
        self.timer_channel=t.channel(timer_channel,pyb.Timer.PWM, pin=self.servo_pin)  #start PWM on the timer channel for the pin


                 
    def set_pos(self,angle):
        PWM_angle=(angle/180)*2000+500     #converts an angle in degrees to the pwm needed for the servo controller. 500 microseconds 
                                            # is 0 degrees, 2500 is 180 degrees
        self.timer_channel.pulse_width(PWM_angle)

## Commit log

2024-03-08 servo drive
2024-03-09 made a main code and moved files
    this is using the lab 3 code to plot the step response of a 180
    the encoder wires were swapped so I had to just change the sign and it worked
    make sure to copy files over from the board from this folder and not directly from the board
    [controller.py, encoder_reader.py, lab3_main.py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]
2024-03-09 Update main.py
    this is for testing the set points and not to be used on the nucleo board
2024-03-09 created PD controller
    made a PD controller and then a PID with some test code but I think the PID is unnecessary since we are doing control on position and integral of position is idk exactly
2024-03-10 PD Control, Testing GUI, and Camera Algorithim
    When you get the chance you should boot up test_camera_control.py
    -Made PD control for the robot
    -added a GUI where we can test different Kp, Kd, and Setpoint for testing
    -implement the search algorithm for the robot in the mlx_cam file which is stored on the robot
    still required:
    -tuning
    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
2024-03-11 project_main first test
    the device spins around, takes an image, and shoots
    it doesnt really hit the target unfourtunately but thats okay
    could do take an image_blocking code, in a seperate task this would allow us to do the setup as the camera is moving
2024-03-11 Create ME_405 Calculations.xlsx
    [ME_405 Calculations.xlsx]
2024-03-11 project_main additions
    [ME_405 Calculations.xlsx]
2024-03-11 small modificiations
    added some functionality to gui_tuning and re-enabled step_response on the pd_controller.
    need to put all the new files on the board for testing
    added a test_project_main to attempt only one control task and easier to use values
    this could be used for scheduling if we want to
2024-03-11 moved files and created a scheduler
    the scheduler doesn't have the same testing functions but it should hopefully work for implementing our code a fraction faster but will require tuning
    coding is better with friends because they can think about things differently and check your work!
    [mlx_cam.py, scheduler_test.py, test_camera_control.py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]
2024-03-12 Create CPU Holder v4.stl
    [CPU Holder v4.stl]
2024-03-12 changes to mlx_cam calculations
    changed the center of the camera for calculations
    [ME_405 Calculations.xlsx]
2024-03-13 testing 3/12
    [ME_405 Calculations.xlsx]
2024-03-13 cleaning up the code
    cleaned up the project main file and added some comments to the other mlx_cam file
    [ME_405 Calculations.xlsx]
2024-03-13 modified mlx_cam
    added ability to remove artifacts from the camera data
    [ME_405 Calculations.xlsx]
2024-03-14 edited pd_controller and mlx_cam
    changed Kd_controller to use the timer ticks from utime instead of a set amount
    change mlx_cam to take the average of two indexes instead of three and removed the top limit of the get_hotspot calculator
    need to ask how to add the get_hotspot calculation to our doxygen stuff
2024-03-15 changes after tournament
    made some in class changes to MLX cam and project_main
    also need to ask Prof about MLX_cam
    [ME_405 Calculations.xlsx]
2024-03-20 doxy upload and comments
    first doxygen upload and comments for the final report
    [CPU Holder v4.stl]
